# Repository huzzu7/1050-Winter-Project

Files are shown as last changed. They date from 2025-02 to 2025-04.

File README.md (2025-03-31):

# Lulzbot Taz Pro Enclosure

An open-source smart enclosure designed for the Lulzbot Taz Pro made to cost under $150CAD (\~$105USD), featuring a particle filtration and camera system, each costing under $50CAD (\~$35USD).

This was originally designed for [Western University's Free Appropriate Sustainability Technology (FAST) Lab.](https://www.appropedia.org/FAST) But effort has been made in the open sourcing of this project towards the ease of replication. 

The materials used to build this enclosure can be found globally online and at hardware stores.

## CAD Screenshots

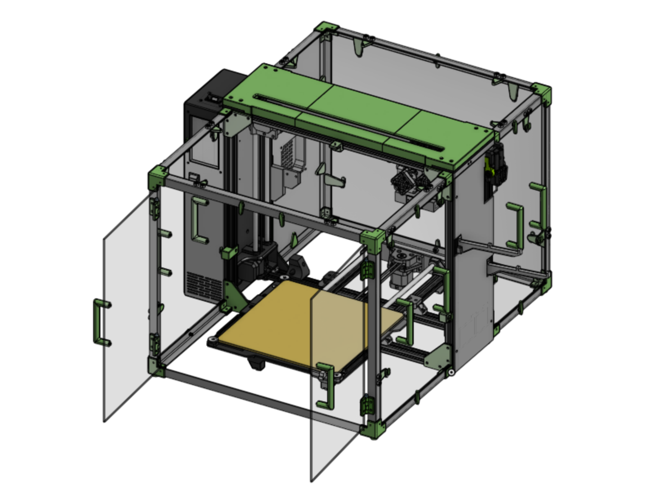
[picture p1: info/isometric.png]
Isometric View


## Team:

[Aaron Mills](https://www.linkedin.com/in/aaron-mills-a40905358/)

[Fady Morgan](https://www.linkedin.com/in/fady-morgan-176a242a2/)

[Gavin Micks](https://www.linkedin.com/in/gavin-micks-5420b3302/)

[Huzaifa Mohammed](https://www.linkedin.com/in/huzaifa-haneef-mohammed/)

[Marcus Morry](https://www.linkedin.com/in/marcus-morry-555574316/")

[Raiden Miyata](https://www.linkedin.com/in/raiden-miyata-463876346/)

[Abbey Jackson](http://linkedin.com/in/abbey-jackson-836358354/)

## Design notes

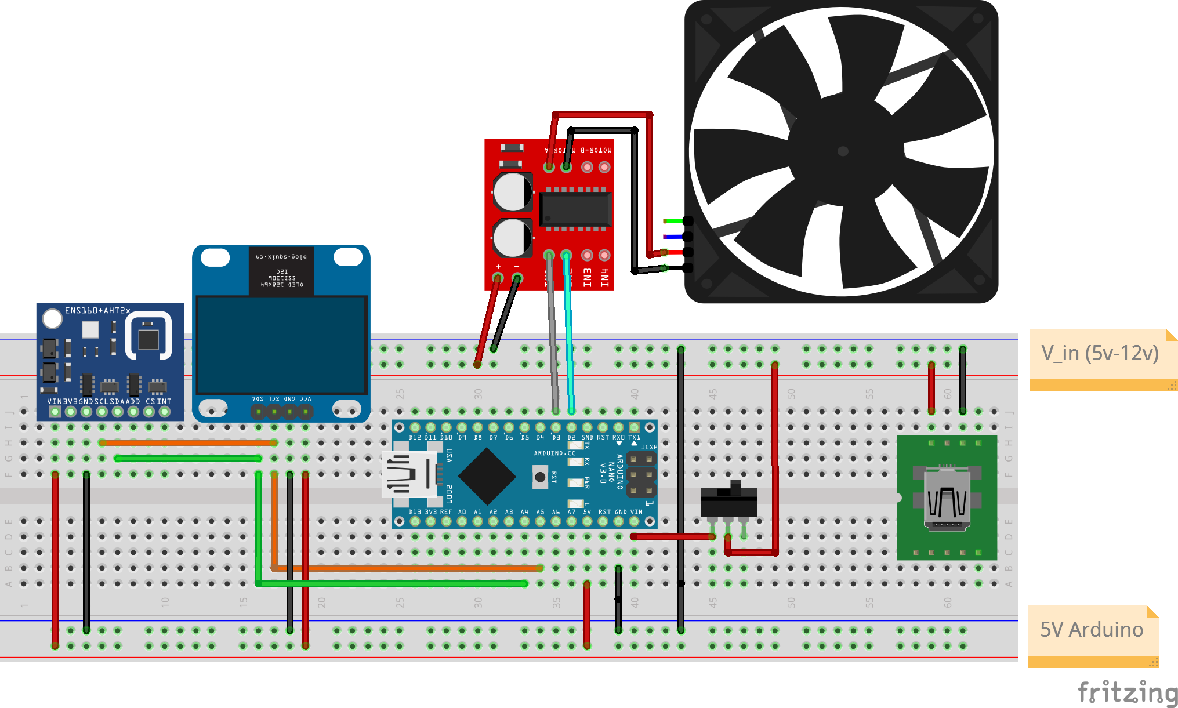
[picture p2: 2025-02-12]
HARDWARE/Schematic_V2_bb.png

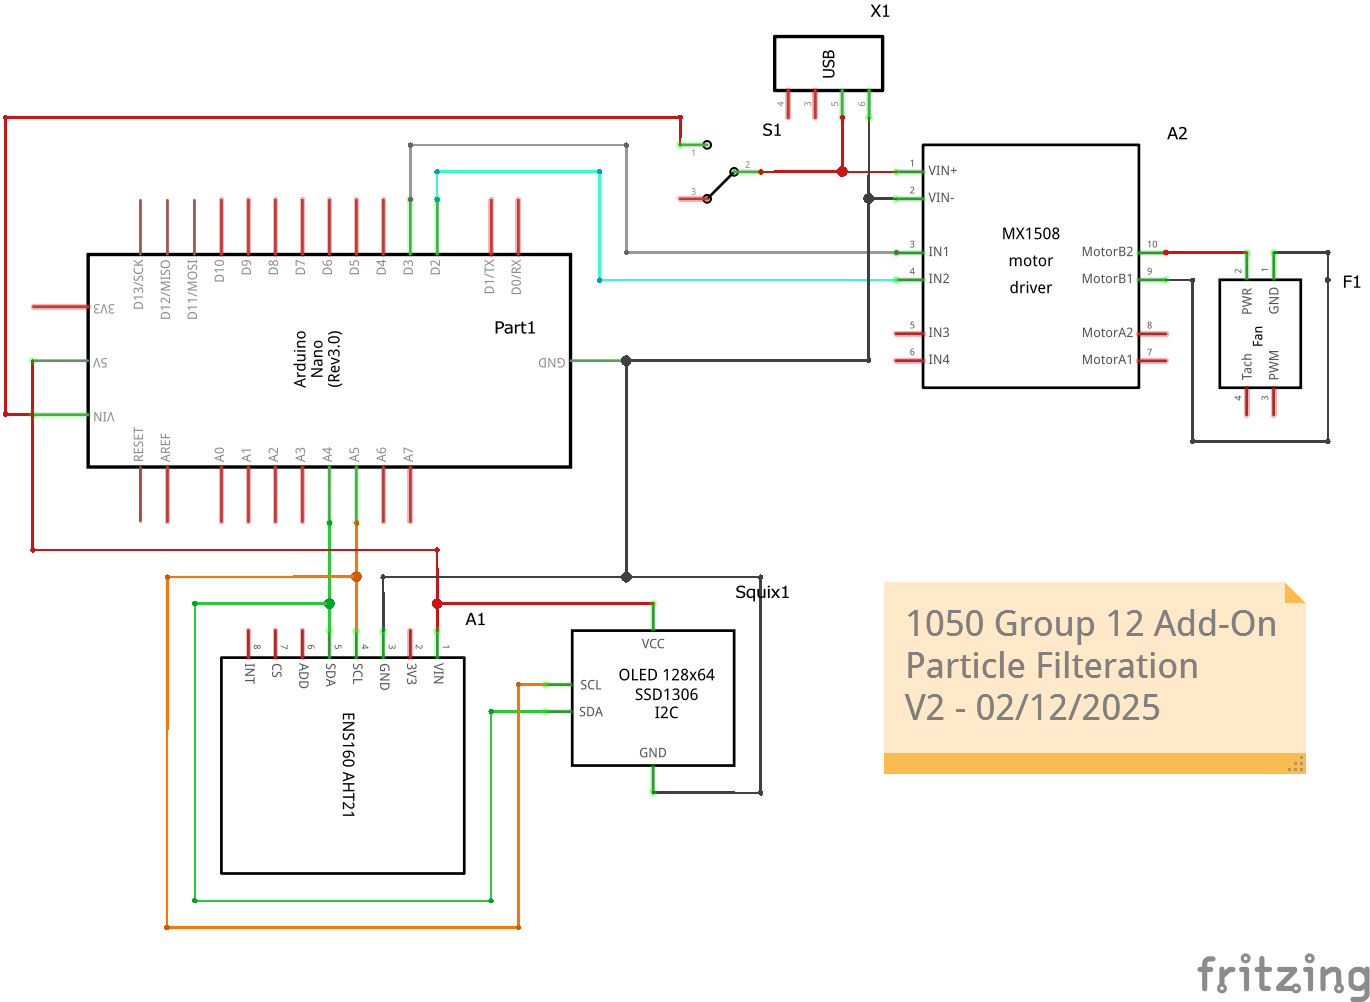
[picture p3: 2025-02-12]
HARDWARE/Schematic_V2_schem.png

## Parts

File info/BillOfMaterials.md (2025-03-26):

# Bill of Materials

A brief description of materials and cost

| #  | Item Description | Units  | Quantity | Unit Cost | Cost  | Source |
|----|---|---|---|---|---|---|
| 1  | Aluminum Angle (3/4", 1/16" thickness) - 8' (243.84cm) | EA | 2 | $15.50 | $31.00 | [Link](https://www.canadiantire.ca/en/pdp/steelworks-solid-aluminum-angle-0616436p.0616436.html) |
| 2  | Aluminum Angle (3/4", 1/16" thickness) - 6' (243.84cm) | EA | 1 | $13.00 | $13.00 | - |
| 3  | 24" x 36" 1/8" Thickness PET Sheet | EA | 3 | $27.50 | $82.50 | [Link](https://www.amazon.ca/gp/product/B09XF2WHYG) |
| 4  | 3D Printing, Own Filament / Printer | g | 1000 | $0.017 | $17.00 | [Link](https://a.co/d/69CIR3W) |
| 5  | Bolts and Nuts Set | EA, KIT| 1 | $35.00 | $35.00 | [Link](https://a.co/d/imsYkwd) |
| 6  | Corrugated Board | EA | 1 | $6.00 | $6.00  | [Link](https://canada.michaels.com/product/plastic-corrugated-board-by-creatology-10567987) |
| **Total** |  |  |  |  | **$184.50** |  |

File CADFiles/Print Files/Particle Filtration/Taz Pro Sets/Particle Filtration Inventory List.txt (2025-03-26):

1x Particle Filtration Assembly
1x Particle Filtration Drawer
1x Particle Filtration Component Cover

Infill:10%
Top & Bottom Thickness: 1.2mm
Wall Thickness: 1.4mm
Mass: 286g
Length: 36.17g
Time: 1 Day 5 Hours 52 Minutes

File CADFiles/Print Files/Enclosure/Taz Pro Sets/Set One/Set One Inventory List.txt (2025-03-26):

10x Swivel Locks
10x Static Attachment Brackets
4x Top Corner Brackets
4x Bottom Corner Brackets
2x Top Panel Holders
2x Left Frame Hooks
1x Right Frame Hooks
7x Top Hooks
3x Right Hooks
2x Left Hooks

Infill: 20%
Mass: 335g
Length: 42.30m
Time: 1 Day 14 Hours 22 Minutes

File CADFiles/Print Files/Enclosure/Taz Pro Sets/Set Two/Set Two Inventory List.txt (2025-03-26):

10x Handles
20x Handle Bolts
60x Nuts
1x Top Centre Front
1x Top Centre Back

Infill: 20%
Mass: 298g
Length: 37.65m
Time: 1 Day 5 Hours 18 Minutes

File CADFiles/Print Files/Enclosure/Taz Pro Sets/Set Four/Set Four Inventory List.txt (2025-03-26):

1x Top Right

Infill: 20%
Mass: 132g
Length: 16.66m
Time: 11 Hours 21 Minutes

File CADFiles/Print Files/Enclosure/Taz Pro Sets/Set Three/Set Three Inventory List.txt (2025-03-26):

1x Top Left

Infill: 20%
Mass: 132g
Length: 16.66m
Time: 11 Hours 18 Minutes

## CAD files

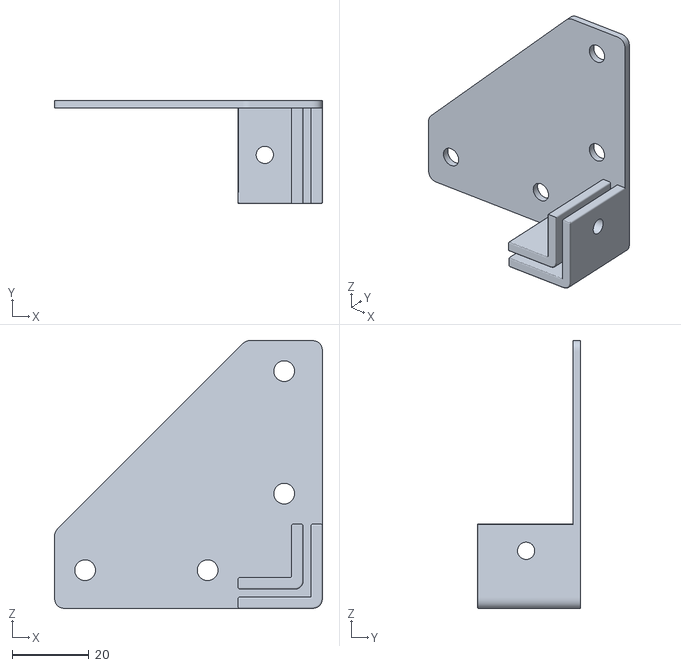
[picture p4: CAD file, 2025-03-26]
CADFiles/Print Files/Enclosure/Frame Attachment Brackets - Attachment Brackets.stl
70.0 x 27.0 x 70.0

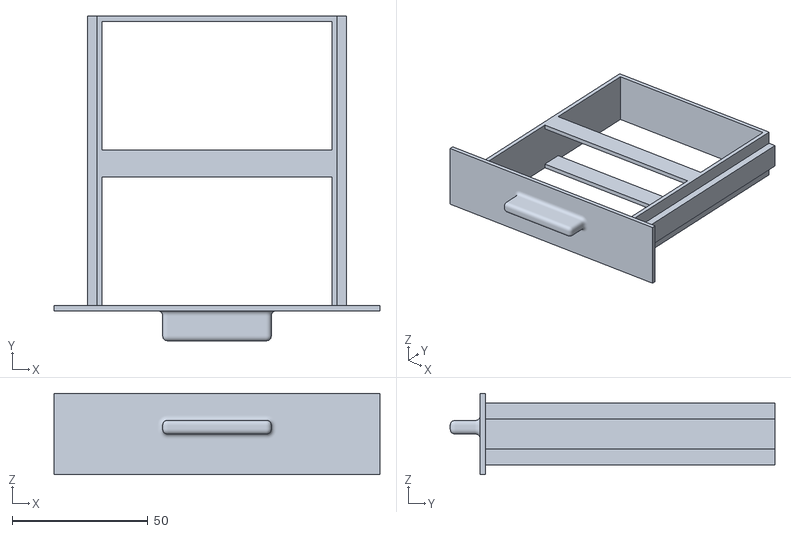
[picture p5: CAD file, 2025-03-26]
CADFiles/Print Files/Particle Filtration/Particle Filtration Drawer.stl
120.0 x 119.5 x 30.0

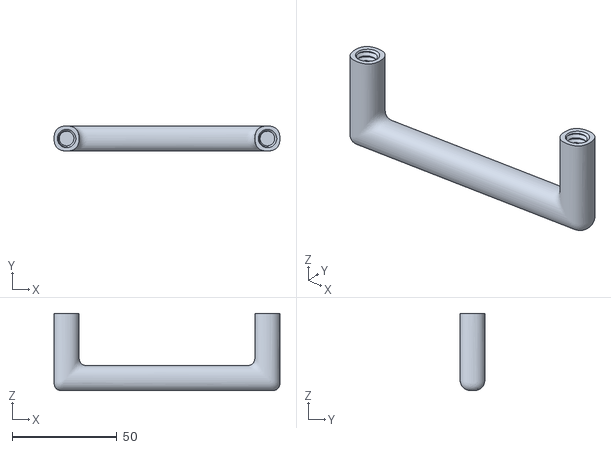
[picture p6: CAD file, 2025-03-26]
CADFiles/Print Files/Enclosure/Handle.stl
108.0 x 12.0 x 37.0

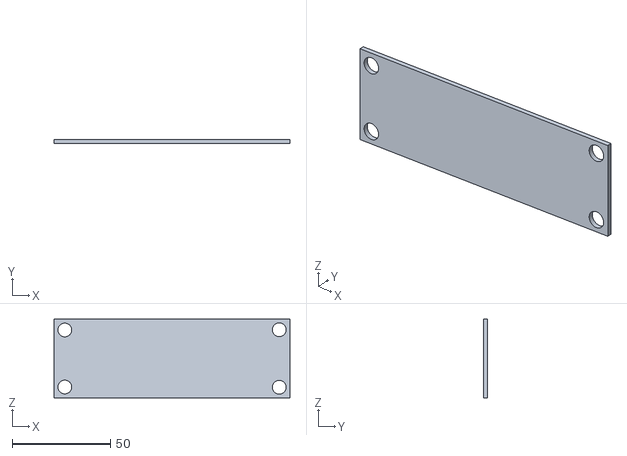
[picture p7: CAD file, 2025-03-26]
CADFiles/Print Files/Particle Filtration/Particle Filtration Component Cover.stl
120.0 x 2.00 x 40.0

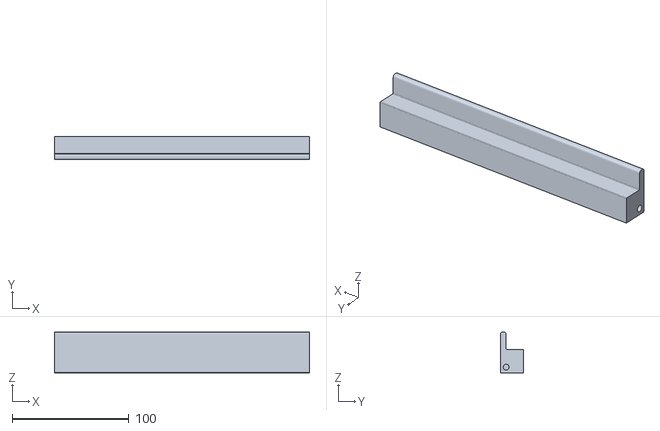
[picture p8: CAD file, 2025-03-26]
CADFiles/Print Files/Enclosure/3D Printed Top - V2 - Center Front.stl
218.0 x 20.0 x 35.0

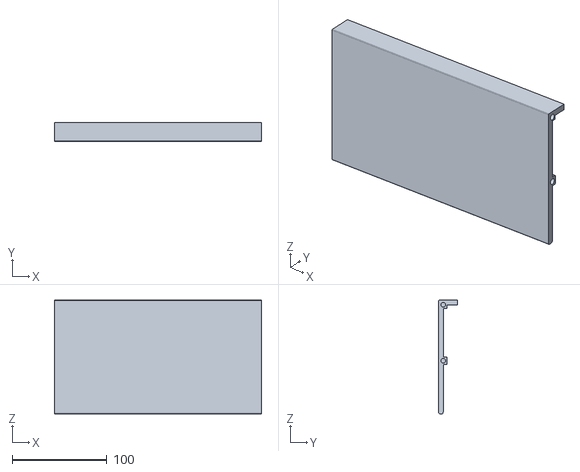
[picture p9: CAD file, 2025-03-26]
CADFiles/Print Files/Enclosure/3D Printed Top - V2 - Center Back.stl
218.0 x 20.0 x 120.0

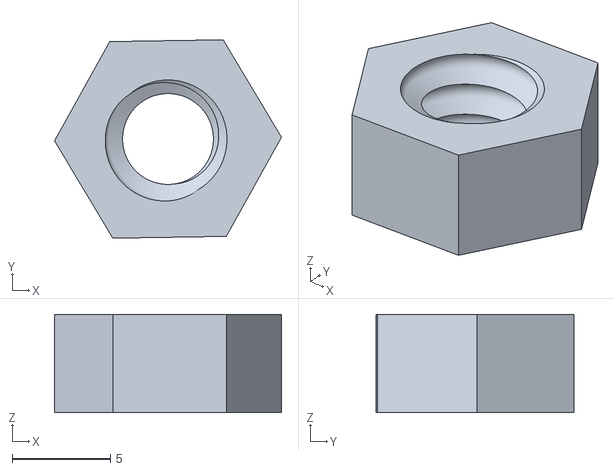
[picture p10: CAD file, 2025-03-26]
CADFiles/Print Files/Enclosure/Generic Nut - 6D - Nut.stl
11.5 x 10.1 x 5.00

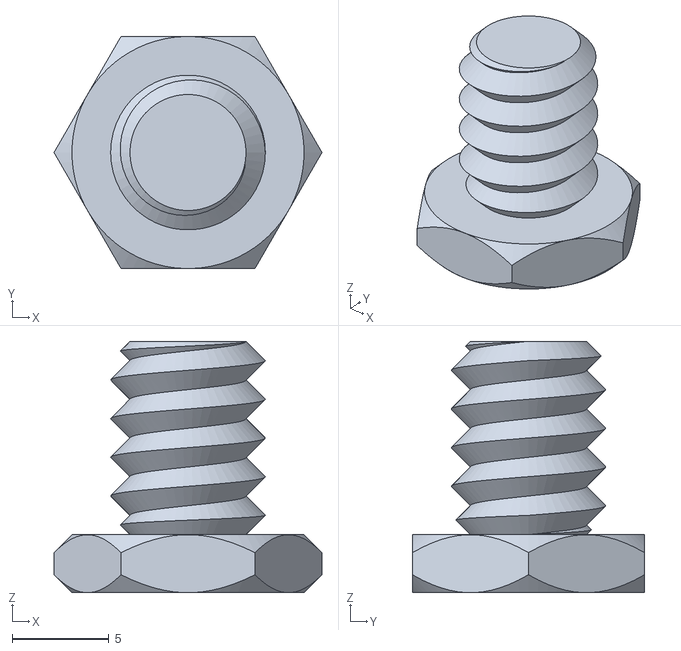
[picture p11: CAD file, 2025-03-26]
CADFiles/Print Files/Enclosure/Handle Nut.stl
13.9 x 12.0 x 13.0

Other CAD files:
CADFiles/Print Files/Enclosure/Taz Pro Sets/Set Four/Set Four.3mf
CADFiles/Print Files/Enclosure/Taz Pro Sets/Set One/Set One - Cura.3mf
CADFiles/Print Files/Enclosure/Taz Pro Sets/Set Three/Set Three.3mf
CADFiles/Print Files/Enclosure/Taz Pro Sets/Set Two/Set Two.3mf
CADFiles/Print Files/Particle Filtration/Taz Pro Sets/Particle Filtration.3mf

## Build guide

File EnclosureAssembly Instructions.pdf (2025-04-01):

# LulzBot TAZ Pro

## Enclosure Assembly

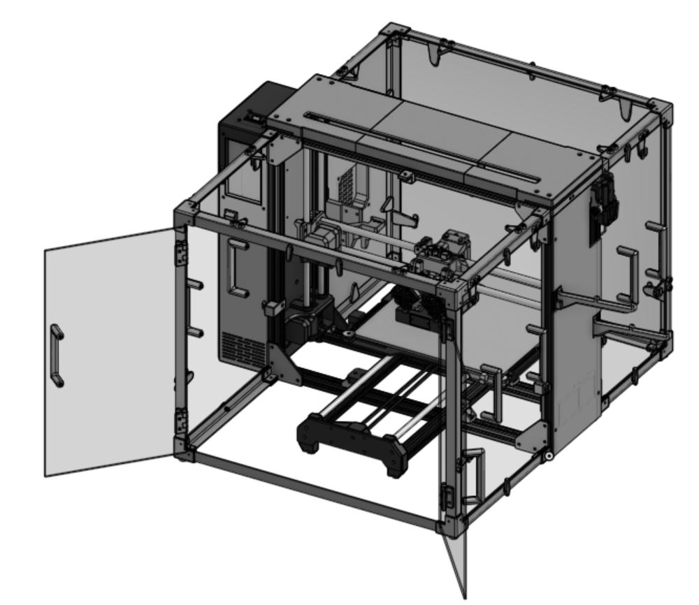
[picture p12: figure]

## WARNING

Safety Precautions
PERSONAL PROTECTIVE EQUIPMENT
- Wear safety glasses throughout the building process
- Use a dust mask when cutting and sanding components MATERIALS HANDLING
- Be cautious when handling sharp edges and material corners
- Use gloves when handling and cutting plexiglass to avoid cuts and glass splinters
- Ensure proper ventilation when working with materials that may emit fumes or particles
ASSEMBLY AREA
- Keep workplace clear and free of clutter to prevent accidents
- Ensure adequate lighting to prevent misplaced parts or tools
- Be mindful of trip hazards from tools, cables, or materials FOLLOW INSTRUCTIONS
- Read and understand all assembly instructions before starting
- Seek help if needed (GitHub video resource)
Disclaimer: Following these warnings does not guarantee safety; always exercise caution and use common sense during assembly and operation.

## TOOLS REQUIRED

Utility Knife | Drill (3mm, 6mm, 8mm) | Hacksaw
Needle-Nose Pliers | Bastard File

Metric Allen Key Set

## PREPARE 3D-PRINTED COMPONENTS

Go into the GitHub to access Onshape files needed to print
CORNERS (4 TOP + 4 BOTTOM) | HANDLES (10)
FRAME ATTATCHMENT BRACKET (8) | SWIVEL LOCKS (10)
STATIC ATTATCHMENT | HOOKS (7 Top + 3 Right + 2
BRACKET (12) | Left +2 Frame Left + 1 Frame Right)
Nuts (60)
Top Assembly (1 Right + 1 Centre Front + 1 Centre Back + Left)

## ALUMINUM FRAME

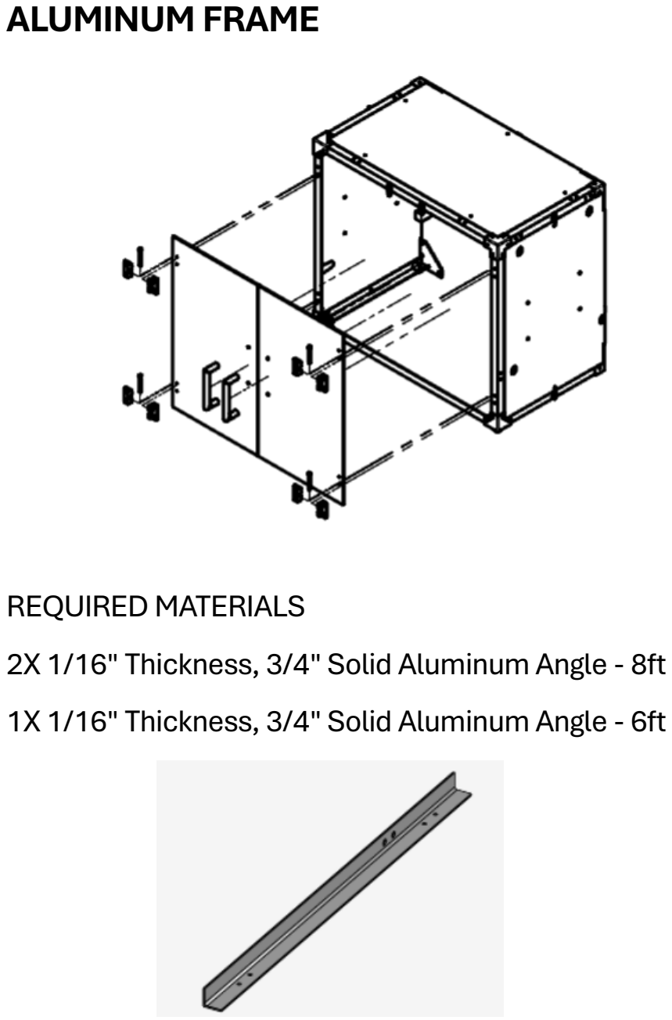
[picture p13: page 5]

REQUIRED MATERIALS
2X 1/16" Thickness, 3/4" Solid Aluminum Angle - 8ft 1X 1/16" Thickness, 3/4" Solid Aluminum Angle - 6ft

Cut and drill holes in the angled aluminum to the following dimensions:

## FRONT WIDTH TOP

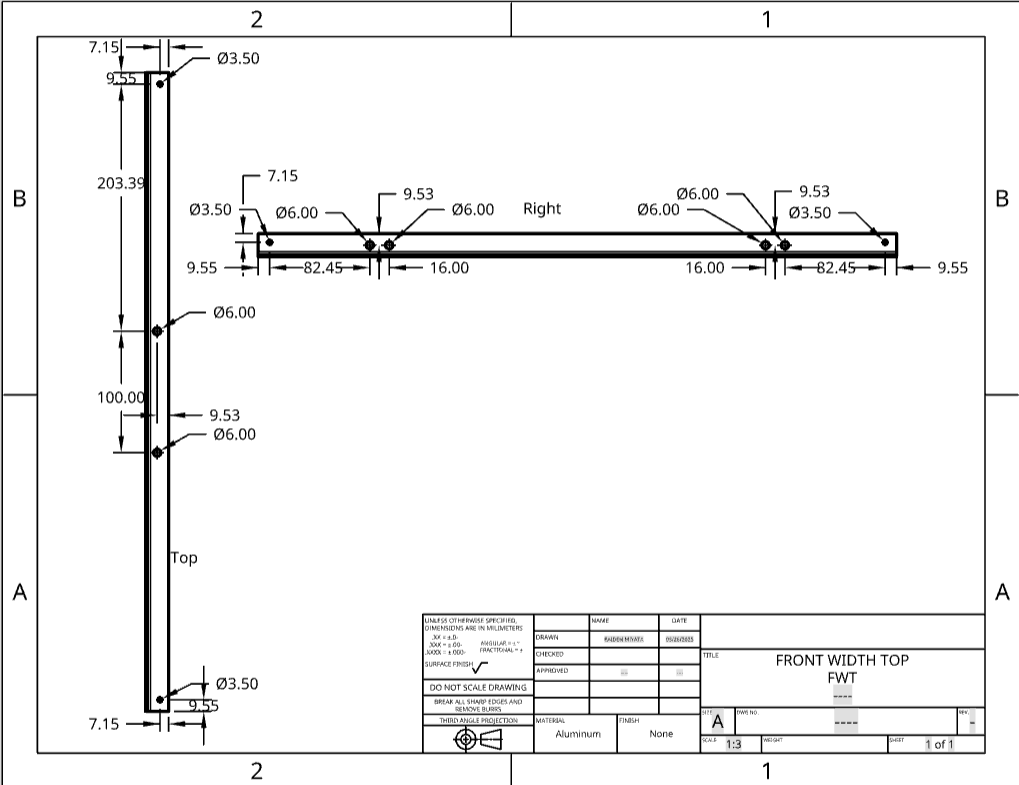
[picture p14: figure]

This drawing is for the width cut of the frame when facing the control panel front-on.

## FRONT LENGTH BOTTOM

This drawing is for the lower length cut of frame when facing the control panel front-on.

## FRONT LENGTH TOP RIGHT

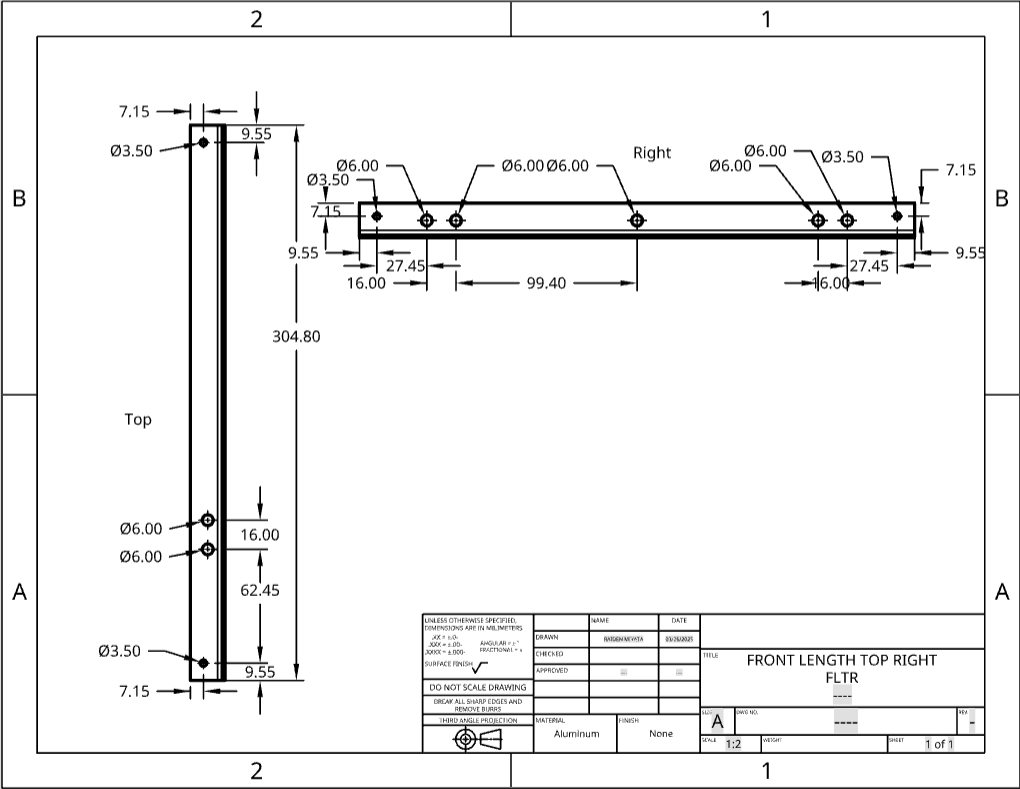
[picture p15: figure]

This drawing is for the top right cut of frame going into the printer when facing the control panel front-on.

## FRONT LENGTH TOP LEFT

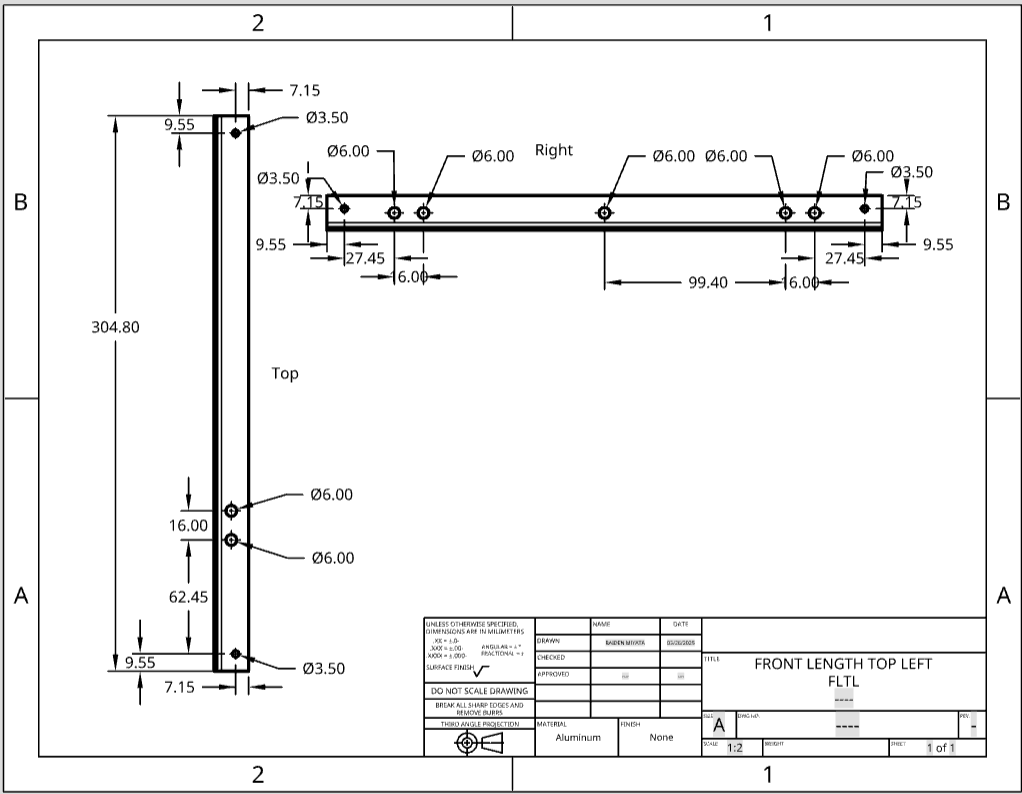
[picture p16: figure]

This drawing is for the top left length cut going inward towards the printer when facing the control panel front-on.

## FRONT WIDTH BOTTOM

This drawing is for the lower width cut of frame going along the length of the printer when facing the control panel front-on.

## FRONT HEIGHT LEFT

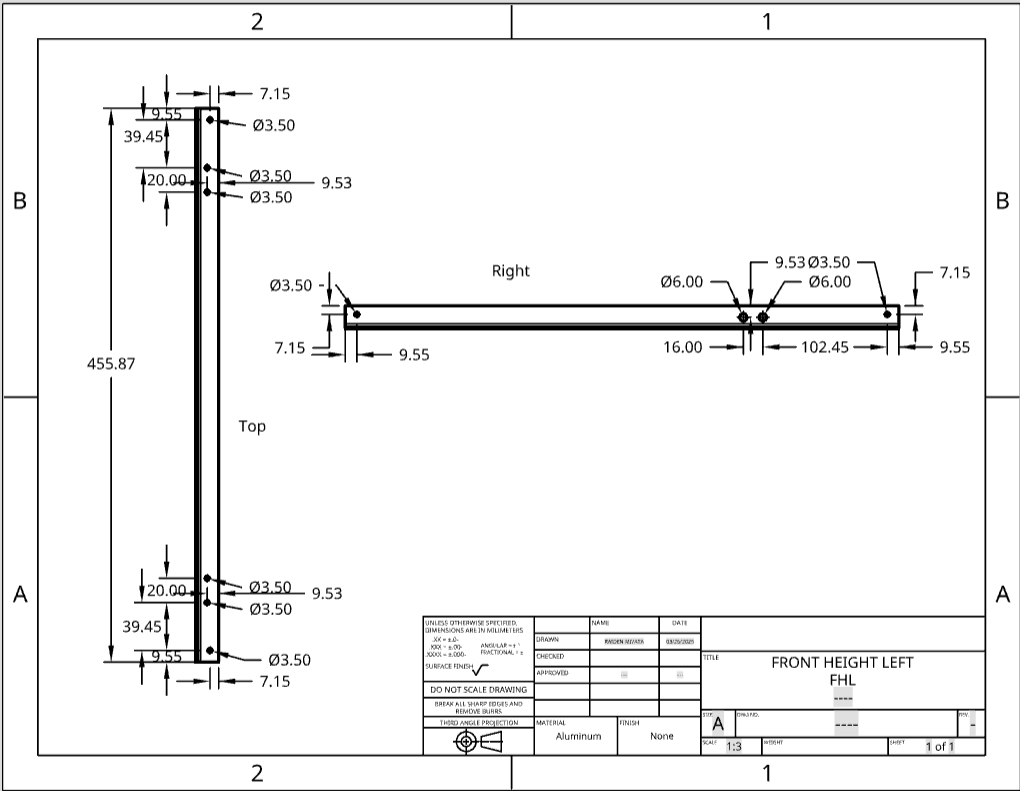
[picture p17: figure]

This drawing is for the left height cut of frame going upward when facing the control panel front-on.

## FRONT HEIGHT RIGHT

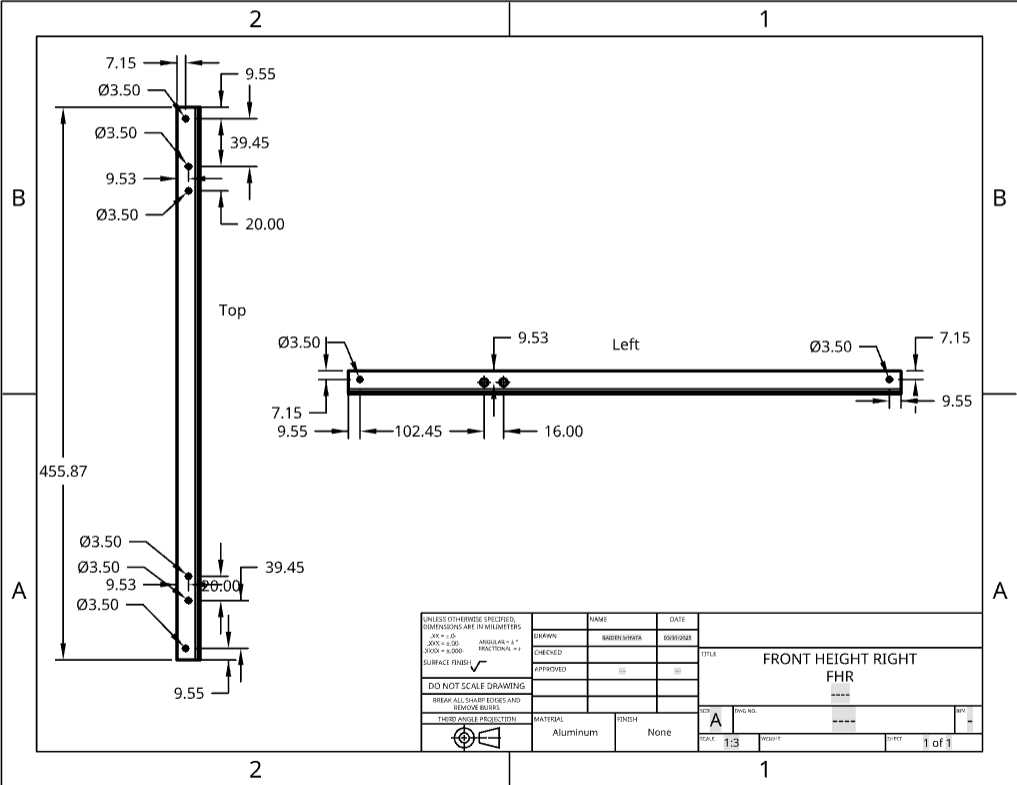
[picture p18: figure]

This drawing is for the right height cut of frame going upward when facing the control panel front-on.

## BACK LENGTH TOP LEFT

This drawing is for the top left length cut of the frame going inward when facing the direct back of the control panel.

## BACK LENGTH TOP RIGHT

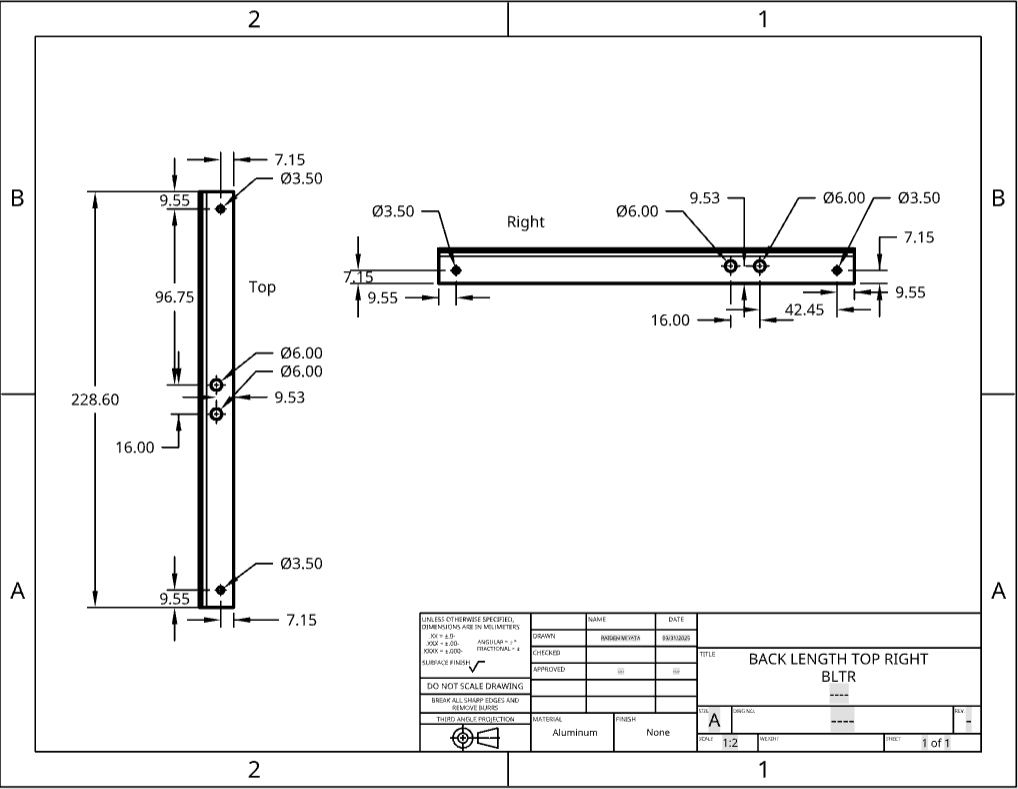
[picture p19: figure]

This drawing is for the top right length cut of the frame going inward when facing the direct back of the control panel.

## BACK LENGTH BOTTOM LEFT

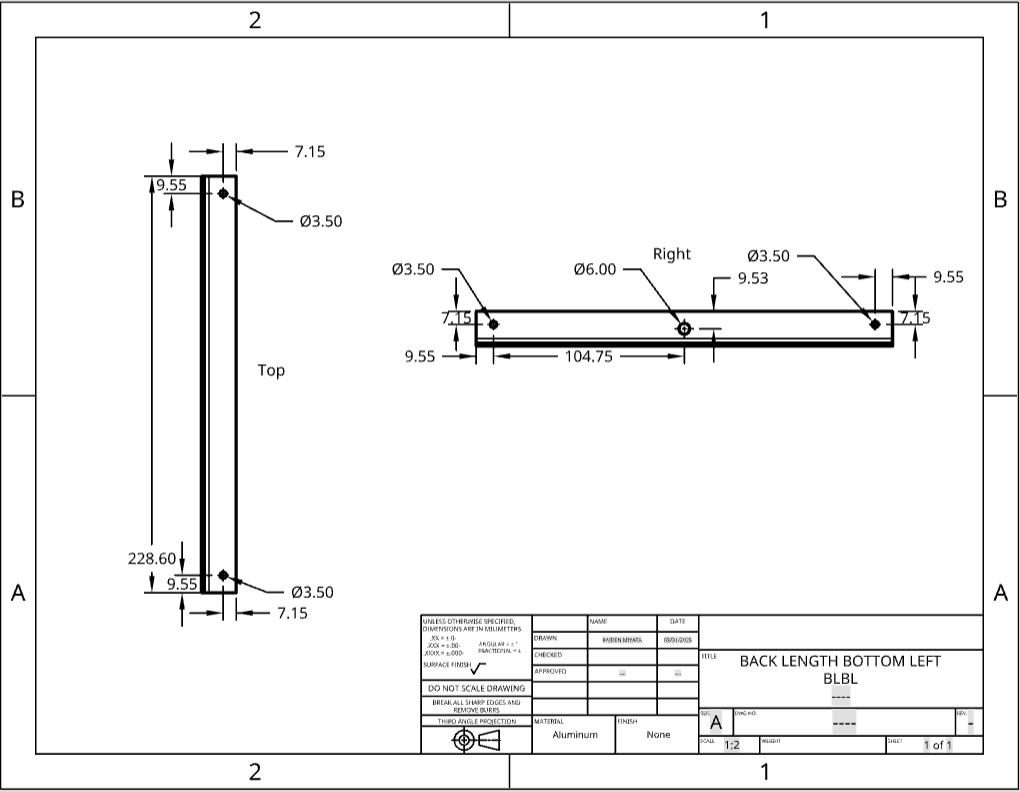
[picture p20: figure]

This drawing is for the bottom left length cut of the frame going inward when facing the direct back of the control panel.

## BACK LENGTH BOTTOM RIGHT

This drawing is for the bottom right length cut of the frame going inward when facing the direct back of the control panel.

## BACK WIDTH BOTTOM

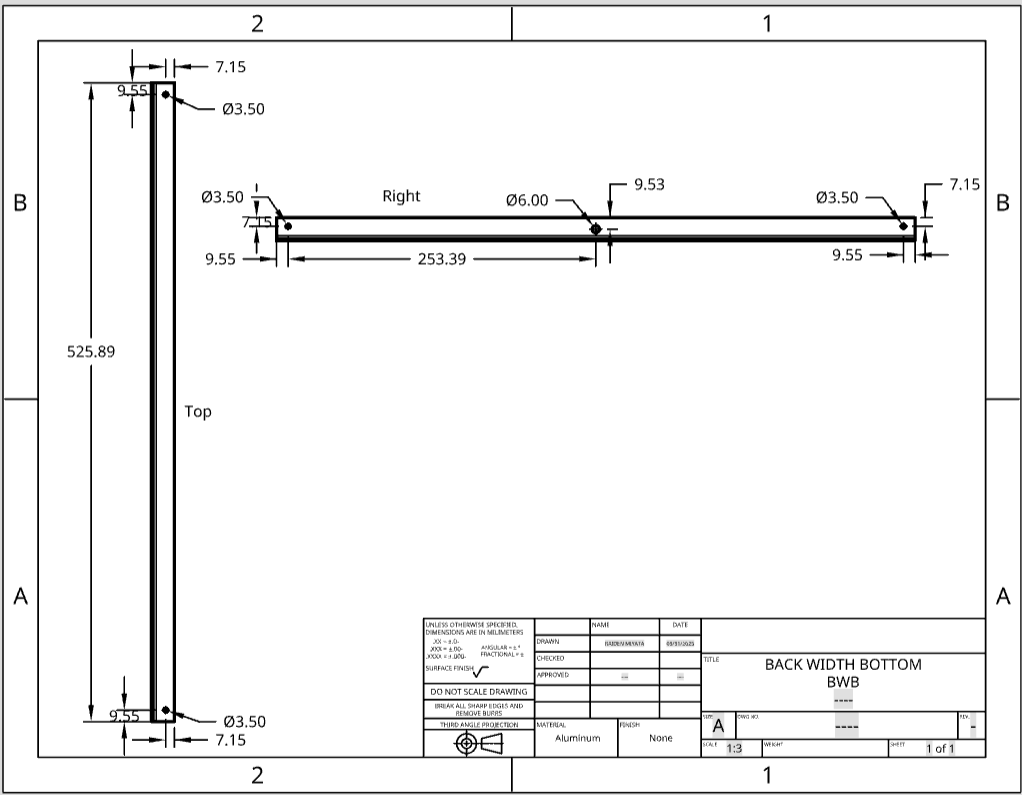
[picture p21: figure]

This drawing is for the bottom width cut of the frame going along the printer when facing the direct back of the control panel.

## BACK WIDTH TOP

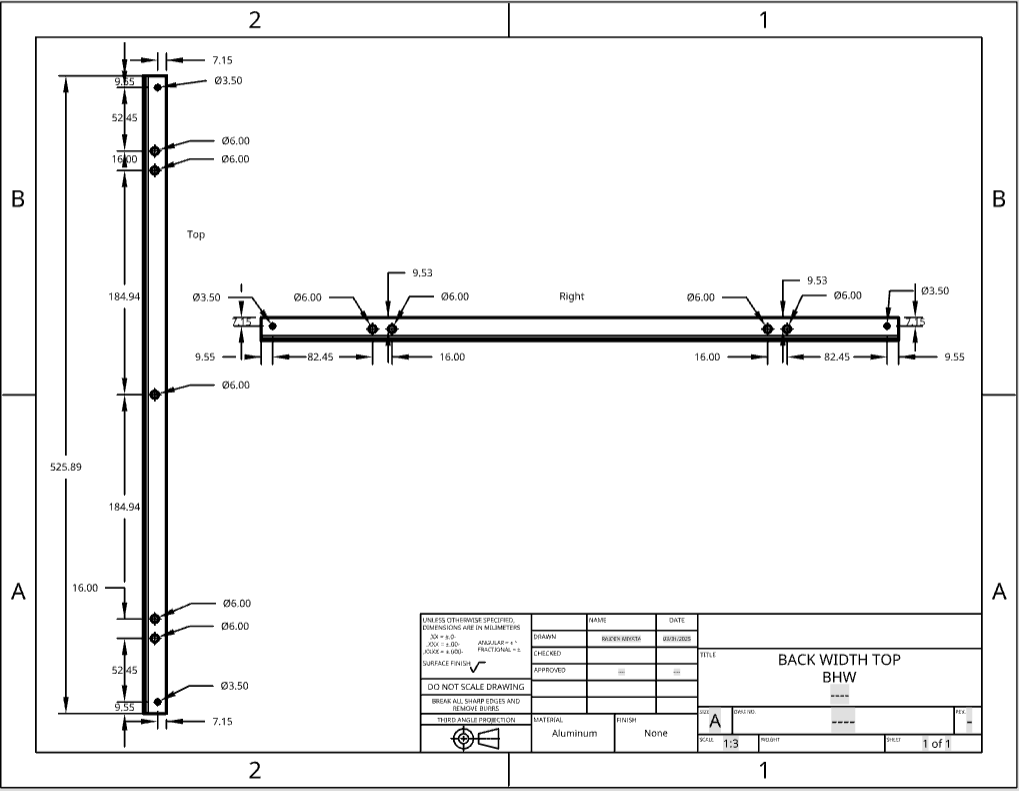
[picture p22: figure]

This drawing is for the top width cut of the frame going along the printer when facing the direct back of the control panel.

## BACK HEIGHT LEFT

This drawing is for the left height cut of the frame going upward when facing the direct back of the control panel.

## BACK HEIGHT RIGHT

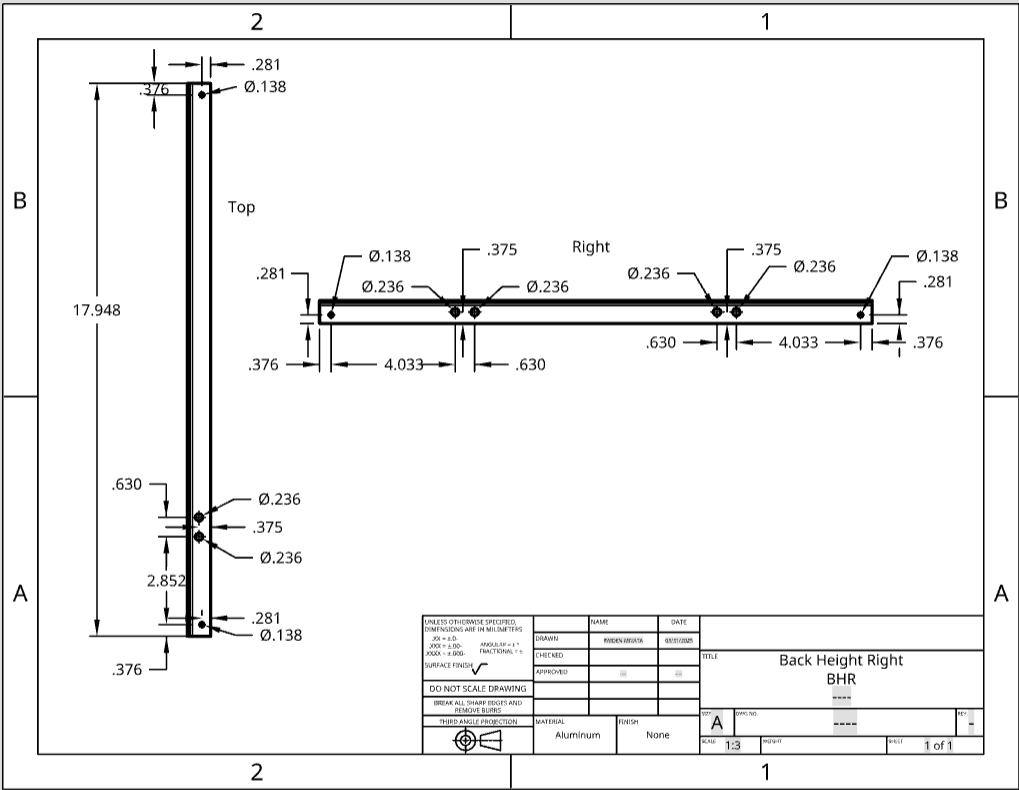
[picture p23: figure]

This drawing is for the right height cut of the frame going upward when facing the direct back of the control panel.

FRONT CORNER ASSEMBLY
BOTTOM CORNERS

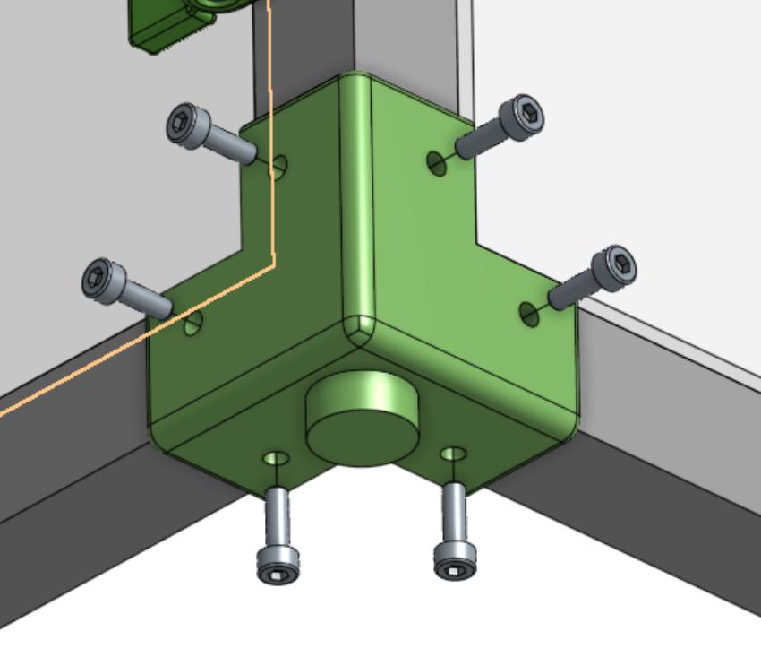
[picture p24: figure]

Acquire the bottom corner parts and insert the angled aluminum into the designed slots. Then screw in the bolts with their assigned nuts.

TOP CORNERS

\

Acquire the top corner parts and insert the angled aluminum into the designed slots. Then screw in the bolts with their assigned nuts.

BACK CORNER ASSEMBLY
BOTTOM CORNERS

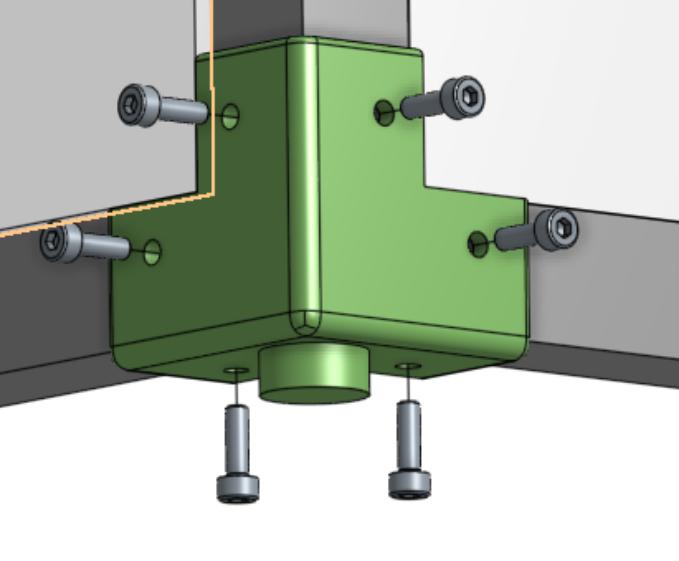
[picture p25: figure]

Acquire the bottom corner parts and insert the angled aluminum into the designed slots. Then screw in the bolts with their assigned nuts.

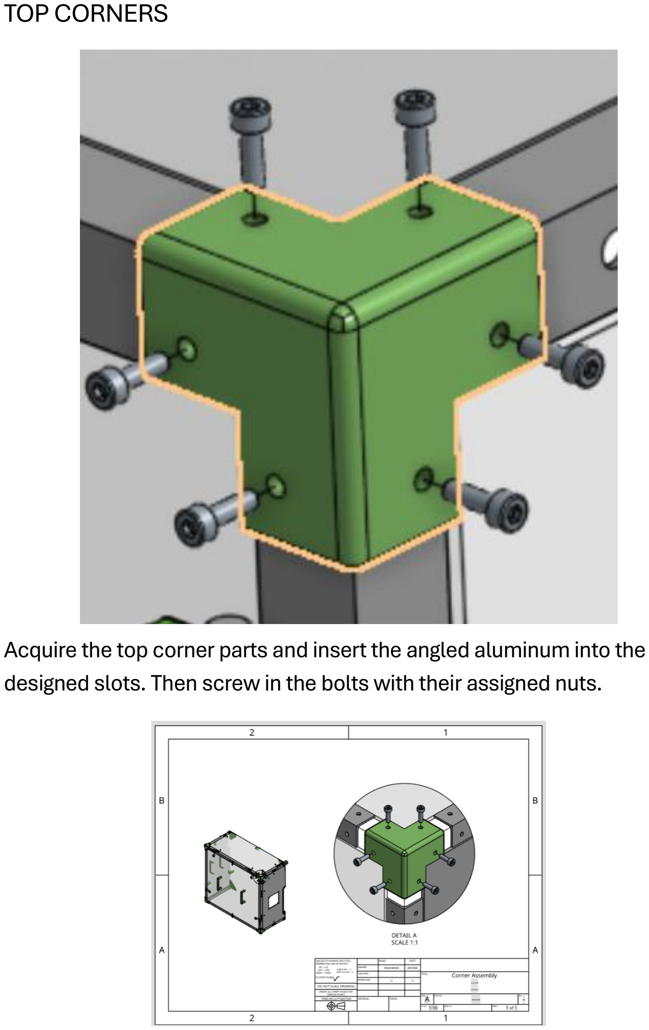
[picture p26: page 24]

TOP CORNERS

Acquire the top corner parts and insert the angled aluminum into the designed slots. Then screw in the bolts with their assigned nuts.

PTG PLASTIC PANELS
Cut and drill holes into the PTG plastic following the drawings below: FRONT TOP

FRONT SIDE

REAR TOP

LARGE REAR

BACK LEFT SIDE

CORROGATED PANELS
PRINTER PANEL

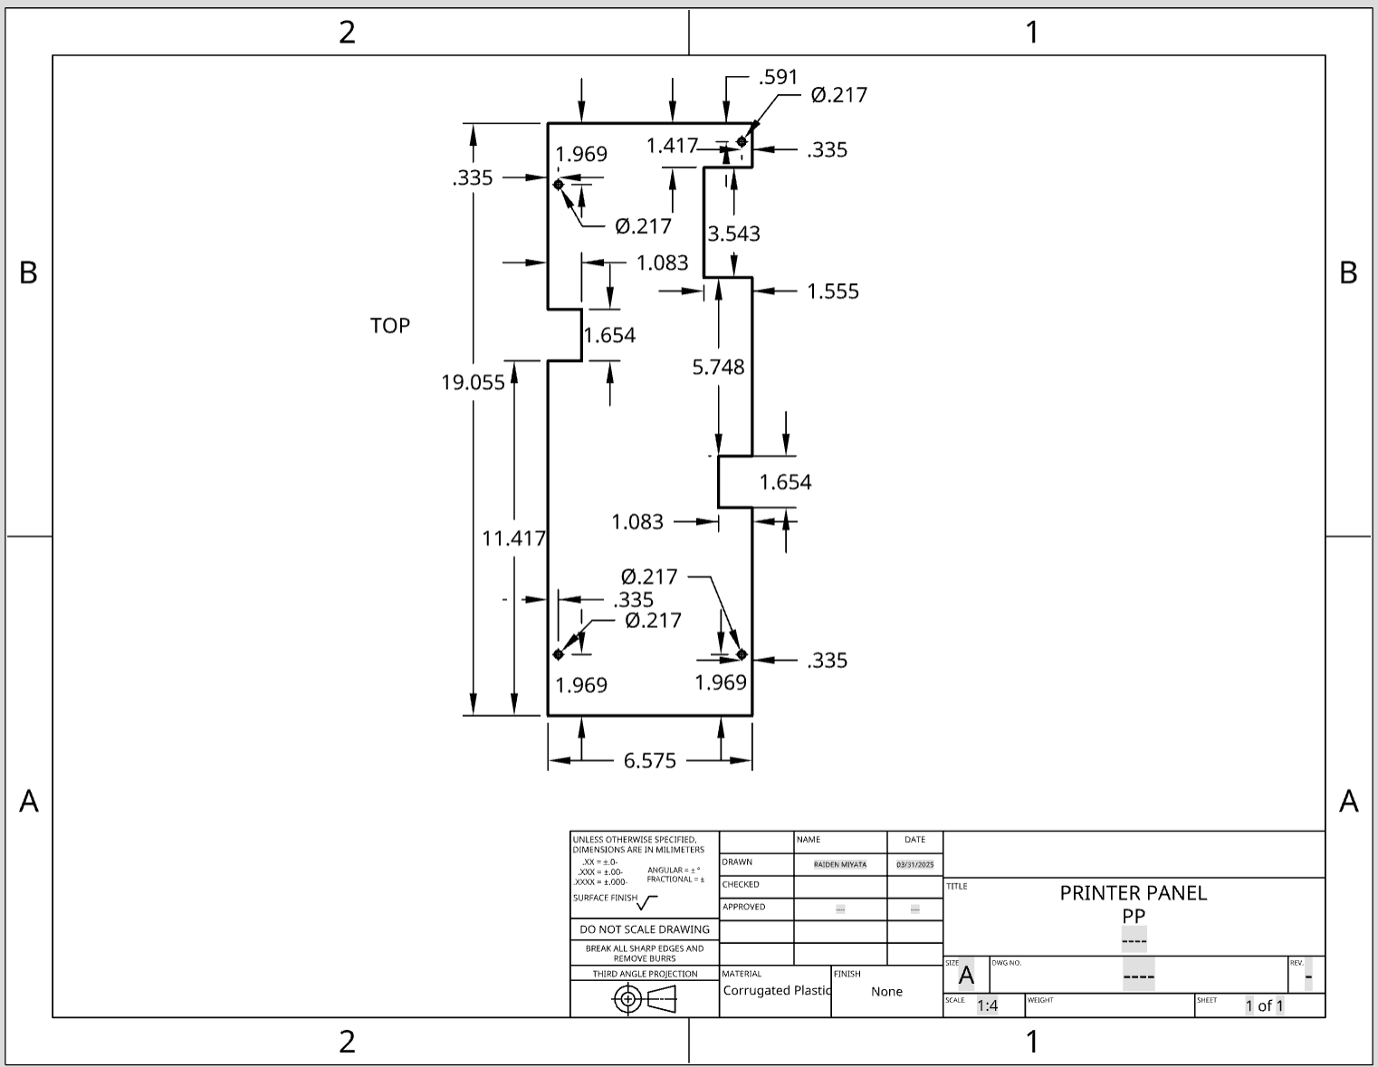
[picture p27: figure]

FAN PANEL

PANEL + FRAME COMPONENTS
Screw in the 3D printed components onto the PTG Panels and aluminum frame as shown in their individual assemblies.

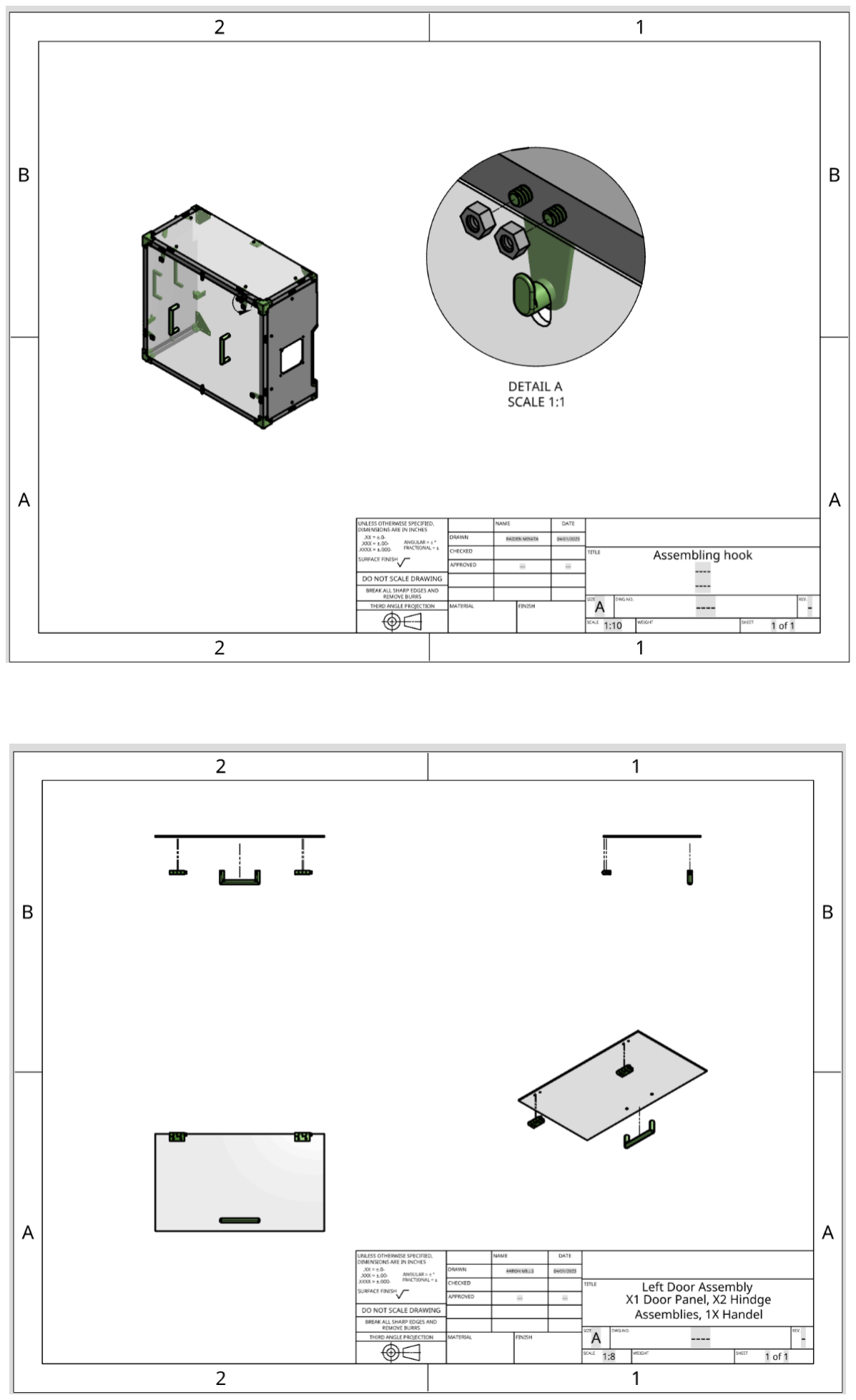
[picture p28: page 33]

DIRECT PRINTER ATTACHMENT
BOTTOM ATTATCHMENT BRACKETS
First attach the brackets to the printer and screw in place, then insert the aluminum frame into the slot and screw that aswell.

TOP ATTATCHMENT BRACKETS
First attach the brackets to the printer and screw in place, then insert the aluminum frame into the slot and screw that aswell.

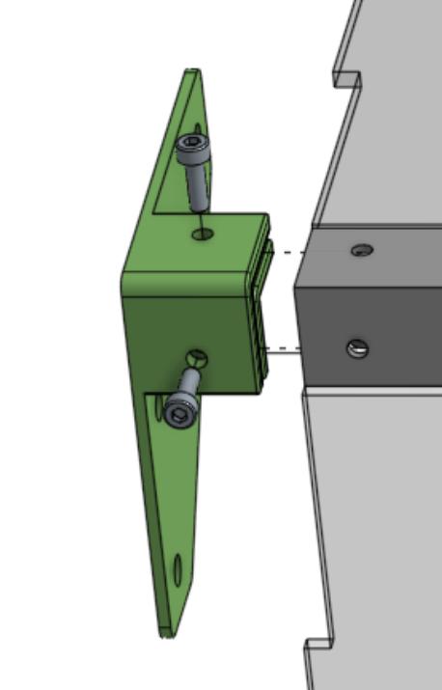
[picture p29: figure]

DIRECT PRINTER ATTACHMENT

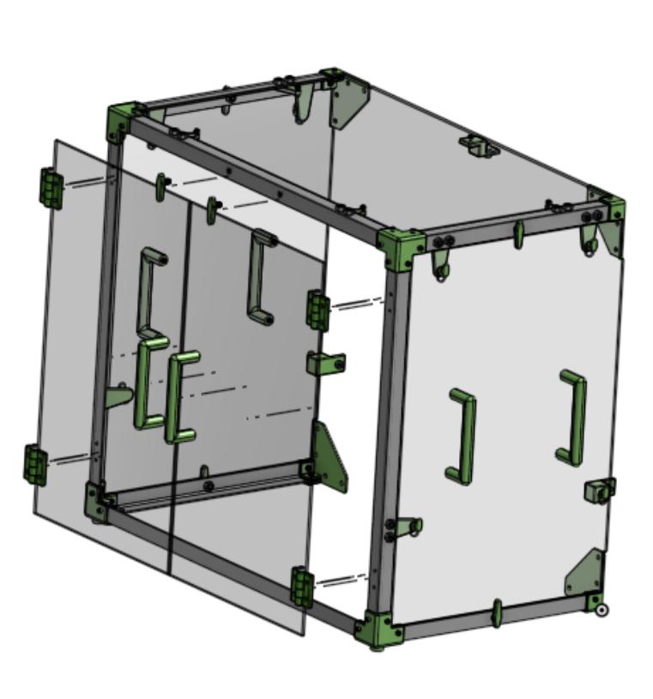
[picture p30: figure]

Using the holes attach the door assemblies to the printer by attaching the hinges to the doors then to their respective holes in the front frame assembly

First attach the static attachment brackets using the 3d printed nuts then place the top panel front resting on them. Then using the respective nuts and bolts attach the panel to the frame

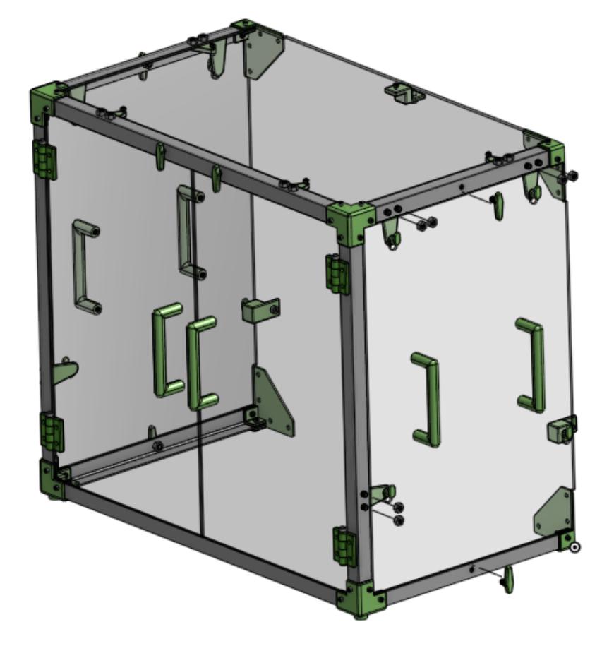
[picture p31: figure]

Attach all the hook and the two swivel locks to the frame using the 3d printed nuts.

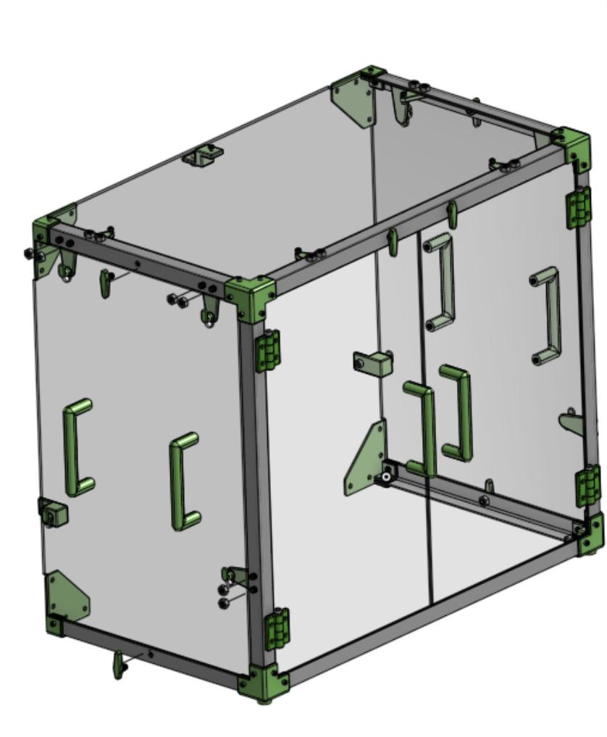
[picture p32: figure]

Attach all the hook and the two swivel locks to the frame using the 3d printed nuts.

For the Large back panel attach all the hooks and swivel locks using the 3d printed nuts.

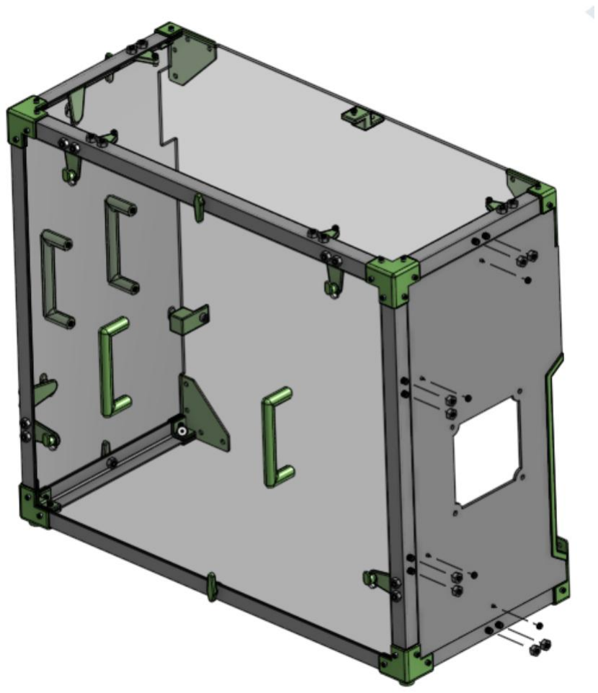
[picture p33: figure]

Using the static attachment brackets use the 3d printed nuts to attach them to the frame then place the panel resting against them. Then use the allocated nuts and bolts to attach the panel to the brackets and frame.

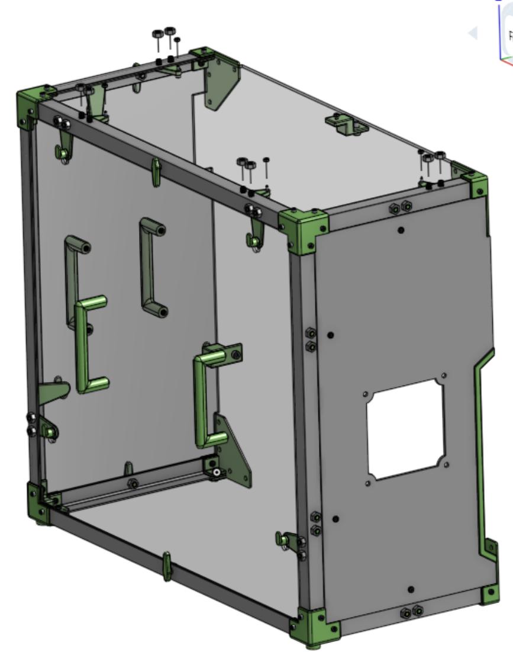
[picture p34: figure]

First attach the static attachment brackets using the 3d printed nuts then place the top panel front resting on them. Using the respective nuts and bolts, attach the panel to the frame.

Using the top parts place the dowels with the holes of the Top centre piece then attach the left and right piece as shown in the photo. The pieces should friction fit however if the fitment is too loose you may always add glue.

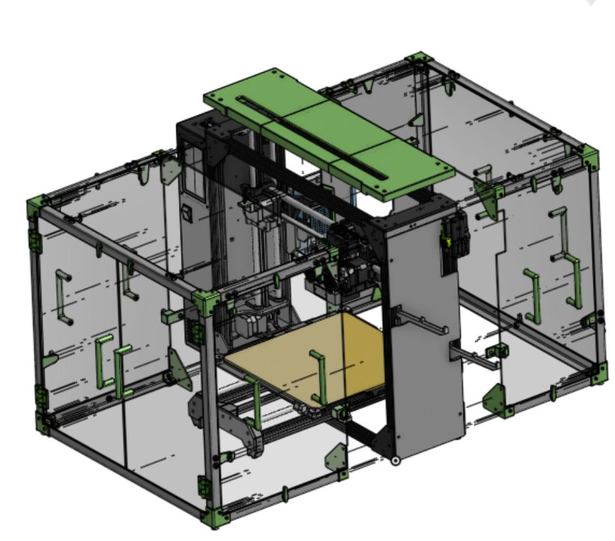
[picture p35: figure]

To attach the front and back frames use the present nuts directly from printer frame. Remove all the nuts and metal plates and line up the metal brackets on the printer to the printed attachment brackets. Reattach the new component with the same nuts the original plates were attached to. For the top remove the bolts which hold the top plates in place, then using the larger bolts attach the Top part by threading the screws through the attachment bracket and into the holes and nuts already there.

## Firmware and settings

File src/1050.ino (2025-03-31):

#include <Wire.h>
#include <Adafruit_GFX.h>
#include <Adafruit_SSD1306.h>
#include "SparkFun_ENS160.h"
#include <Adafruit_AHTX0.h>

// OLED display settings
#define SCREEN_WIDTH 128  // Width of the OLED display in pixels
#define SCREEN_HEIGHT 64   // Height of the OLED display in pixels
#define OLED_RESET -1       // OLED reset pin (not used here)
#define SCREEN_ADDRESS 0x3C // I2C address for the OLED display

// Fan control pin
#define FAN_PIN 10  // Pin used to control the fan speed using PWM

// Initialize OLED display
Adafruit_SSD1306 display(SCREEN_WIDTH, SCREEN_HEIGHT, &Wire, OLED_RESET);
// Initialize ENS160 air quality sensor
SparkFun_ENS160 myENS;
// Initialize AHTX0 temperature and humidity sensor
Adafruit_AHTX0 aht;

// Function to initialize and configure the OLED display
void initializeDisplay() {
    if (!display.begin(SSD1306_SWITCHCAPVCC, SCREEN_ADDRESS)) {
        Serial.println("Display not detected!");
        while (1); // Halt if display initialization fails
    }
    display.setRotation(0);
    display.clearDisplay();
    display.setTextSize(1);
    display.setTextColor(WHITE);
    display.display();
    delay(1000); // Small delay for initialization
}

// Function to initialize the air quality and temperature sensors
void initializeSensors() {
    if (!myENS.begin() || !aht.begin()) {
        Serial.println("Sensor Error!"); // Print error if sensors are not detected
    }
    myENS.setOperatingMode(SFE_ENS160_RESET); // Reset air quality sensor
    delay(100);
    myENS.setOperatingMode(SFE_ENS160_STANDARD); // Set standard operating mode
}

// Function to read sensor data and update the provided variables
void readSensorData(int &TVOC, int &eCO2, int &AQI, sensors_event_t &humidity, sensors_event_t &temp) {
    TVOC = myENS.getTVOC(); // Get Total Volatile Organic Compounds level
    eCO2 = myENS.getECO2(); // Get estimated CO2 level
    AQI = myENS.getAQI();   // Get Air Quality Index
    aht.getEvent(&humidity, &temp); // Get temperature and humidity data
}

// Function to determine the fan speed based on air quality levels
int determineFanSpeed(int eCO2, int TVOC) {
    if (eCO2 > 1200 || TVOC > 500) {
        return 255; // Maximum speed if air quality is poor
    } else if (eCO2 > 800 || TVOC > 300) {
        return 180; // Medium speed for moderate air quality
    } else {
        return 100; // Low speed for good air quality
    }
}

// Function to print sensor data to the Serial Monitor for debugging
void printSensorData(int TVOC, int eCO2, float temperature, float humidity) {
    Serial.print("TVOC: "); Serial.println(TVOC);
    Serial.print("eCO2: "); Serial.println(eCO2);
    Serial.print("Temperature: "); Serial.println(temperature);
    Serial.print("Humidity: "); Serial.println(humidity);
    Serial.println("----------------------");
}

// Function to update the OLED display with sensor readings and fan speed
void updateDisplay(int TVOC, int AQI, int eCO2, float temperature, float humidity, int fanSpeed) {
    display.clearDisplay();
    display.setCursor(0, 0);
    display.print("TVOC   AQI  eCO2");
    display.setCursor(0, 10);
    display.print(TVOC); display.print("ppb  ");
    display.print(AQI); display.print("    ");
    display.print(eCO2); display.print("ppm");
    
    display.setCursor(0, 30);
    display.print("Temp   RH     Fan");
    display.setCursor(0, 40);
    display.print(temperature, 1); display.print("C  ");
    display.print(humidity, 1); display.print("%  ");
    
    int displayFanSpeed = (fanSpeed * 100) / 255; // Convert fan speed to percentage
    display.print(displayFanSpeed); display.print("%");
    
    display.display(); // Update the display
}

// Setup function that runs once at the start
void setup() {
    Serial.begin(9600); // Start serial communication
    Wire.begin(); // Initialize I2C communication
    pinMode(FAN_PIN, OUTPUT); // Set fan pin as output
    
    initializeDisplay(); // Initialize OLED display
    initializeSensors(); // Initialize air quality and temperature sensors
}

// Main loop function that runs continuously
void loop() {
    if (myENS.checkDataStatus()) { // Check if new data is available
        int TVOC, eCO2, AQI;
        sensors_event_t humidity, temp;
        readSensorData(TVOC, eCO2, AQI, humidity, temp);
        
        printSensorData(TVOC, eCO2, temp.temperature, humidity.relative_humidity); // Debugging output
        
        int fanSpeed = determineFanSpeed(eCO2, TVOC); // Get appropriate fan speed
        analogWrite(FAN_PIN, fanSpeed); // Set fan speed using PWM
        
        updateDisplay(TVOC, AQI, eCO2, temp.temperature, humidity.relative_humidity, fanSpeed); // Refresh display
    }
    delay(200); // Short delay before next reading
}

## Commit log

2025-02-12 Added schematic files
    [Schematic_V2.fzz]
2025-03-26 Added material
2025-03-26 Add 3D Files
    [3D Printed Top - V2 - Center Back.stl, 3D Printed Top - V2 - Center Front.stl, Frame Attachment Brackets - Attachment Brackets.stl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]
